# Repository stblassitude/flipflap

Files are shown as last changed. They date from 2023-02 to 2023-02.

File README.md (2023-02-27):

# Controller for OMEGA OM3021 Split-Flap Displays

# Overview
The controller board uses an D1 mini ESP8266 microcontroller to control a number of outputs going to the displays, and read inputs connected to the display encodes, which give the current position of the rotor with the split flaps.

The controller can address 8 lines and 15 columns, for a total of 120 characters. With the displays currently available to us, we're using 6 lines with 11 columns, for a total of 66 characters.

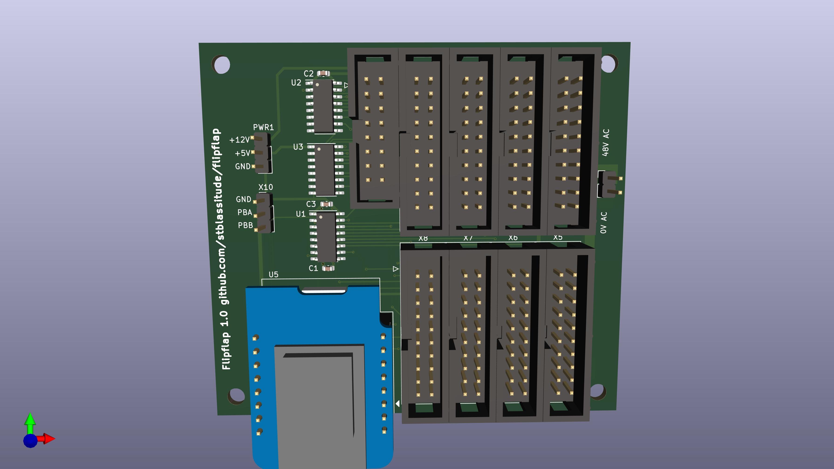
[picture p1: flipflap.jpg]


The schematic [flipflap-sch.pdf](flipflap-sch.pdf) and the assembly diagram [flipflap-pcb.pdf](flipflap-pcb.pdf) show the details of the board.

# Software
An Arduino sketch can be found in [arduino/flipflap](arduino/flipflap).

# Documentation OMEGA OM3021
Documentation for the split-flap display model can be found in [docs/](docs/). [Theory of Operation](docs/theory-of-operation.md) tries to explain how a microcontroller can control the displays.

# Arduino Setup

* https://arduino.github.io/arduino-cli/0.29/getting-started/
* https://medium.com/@thomas.kilmar/arduino-cli-with-visual-studio-code-on-macos-d2ad32ff0276

# Further Reading

We're not the only ones working with these modules.

* [Tim's SplitFlap Clock - Part I (Electronics)](https://web.archive.org/web/20220701175858/https://www.way2.net/2022/03/14/splitflap/). Unfortunately, the software part seems to never have been published.

# Version History

## 1.0

### Known Issues

* /ADC4 to /ADC7 are swapped when looking at the register outputs. This can easily be adjusted in the ADC cable.

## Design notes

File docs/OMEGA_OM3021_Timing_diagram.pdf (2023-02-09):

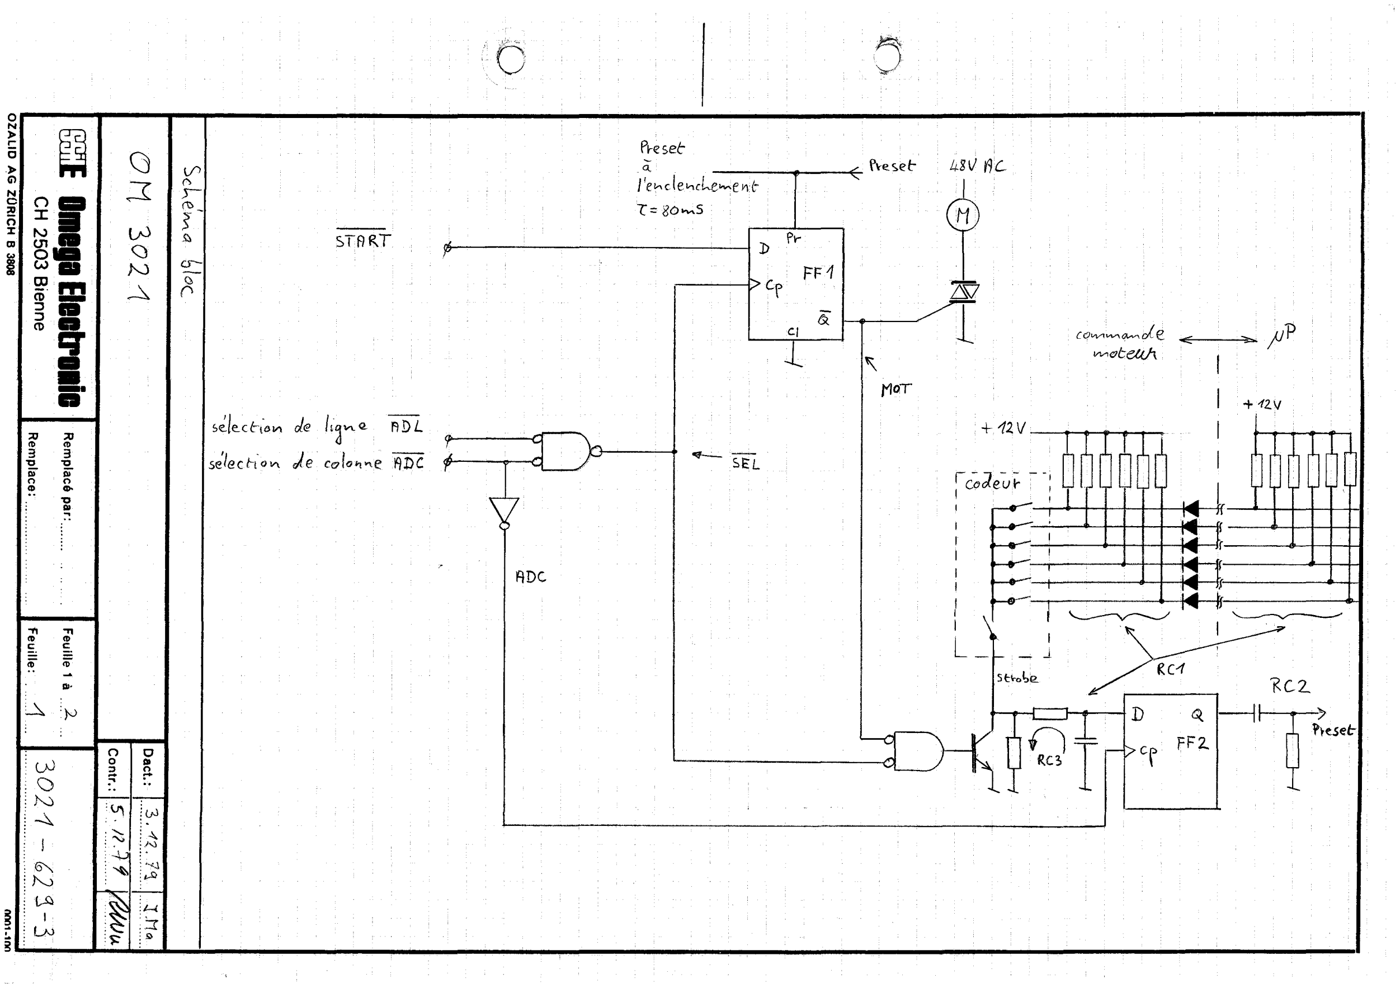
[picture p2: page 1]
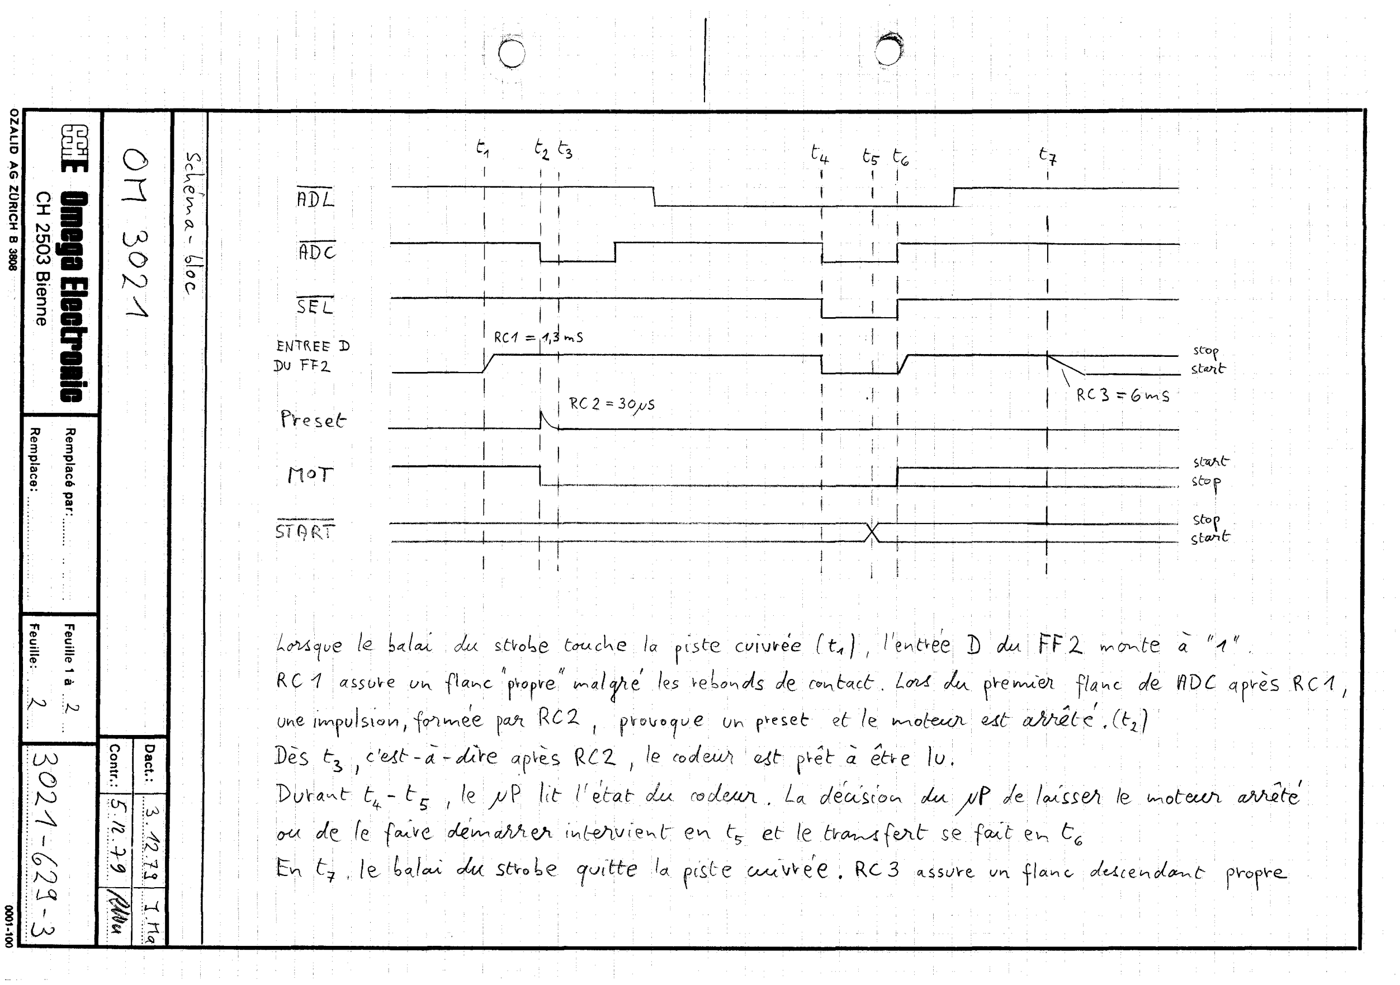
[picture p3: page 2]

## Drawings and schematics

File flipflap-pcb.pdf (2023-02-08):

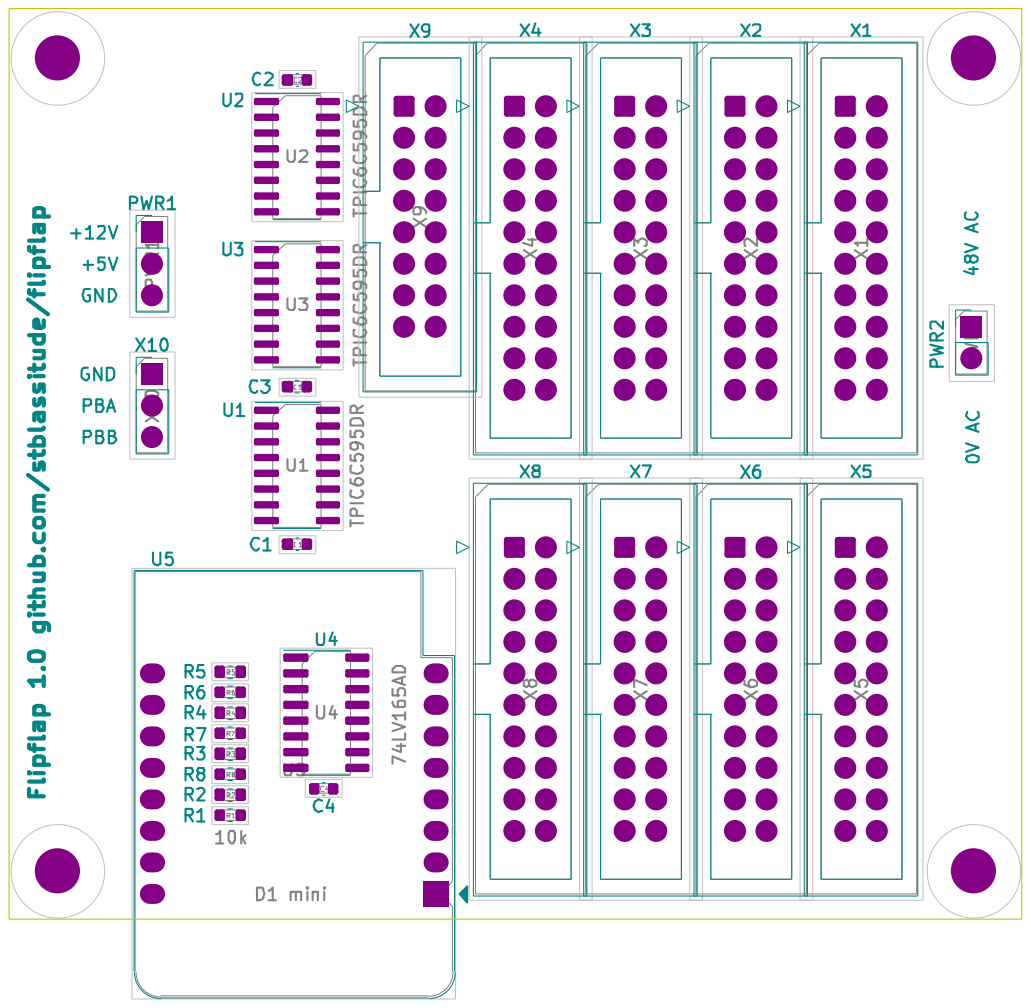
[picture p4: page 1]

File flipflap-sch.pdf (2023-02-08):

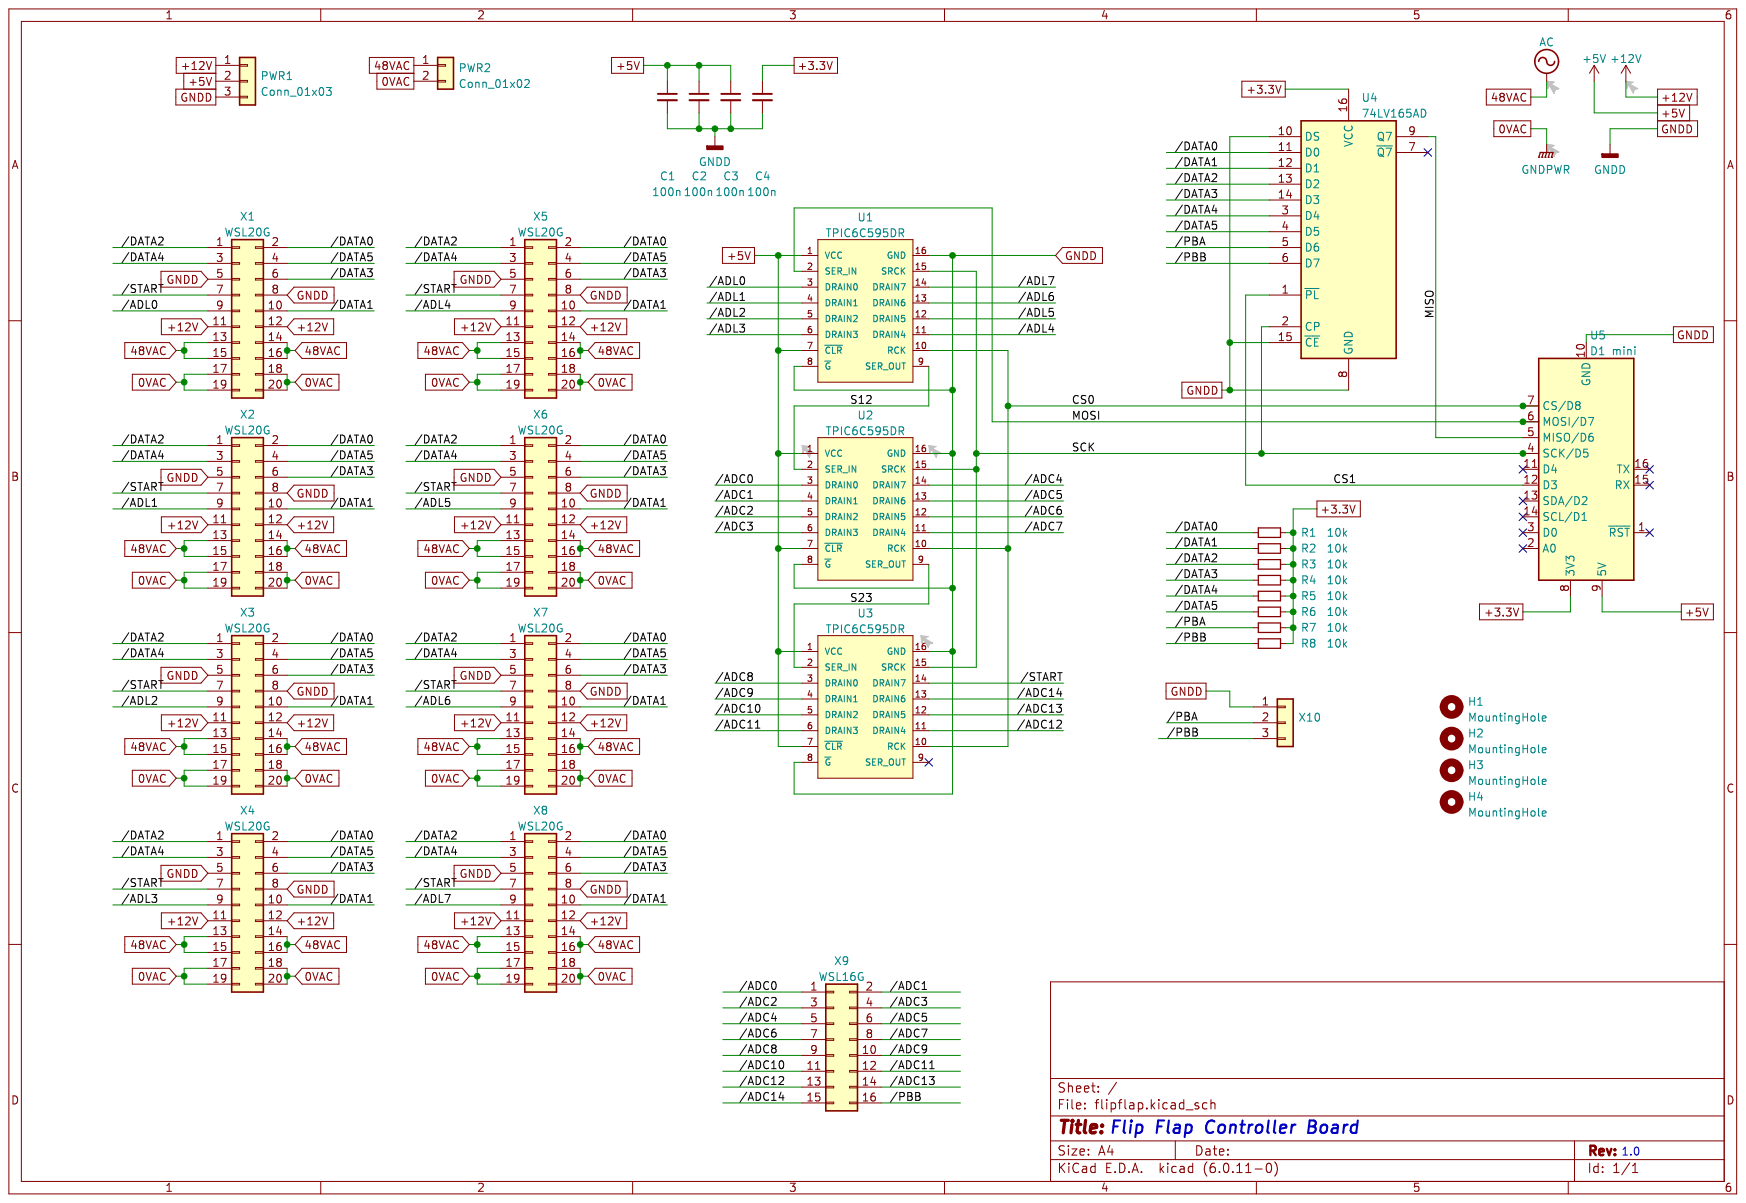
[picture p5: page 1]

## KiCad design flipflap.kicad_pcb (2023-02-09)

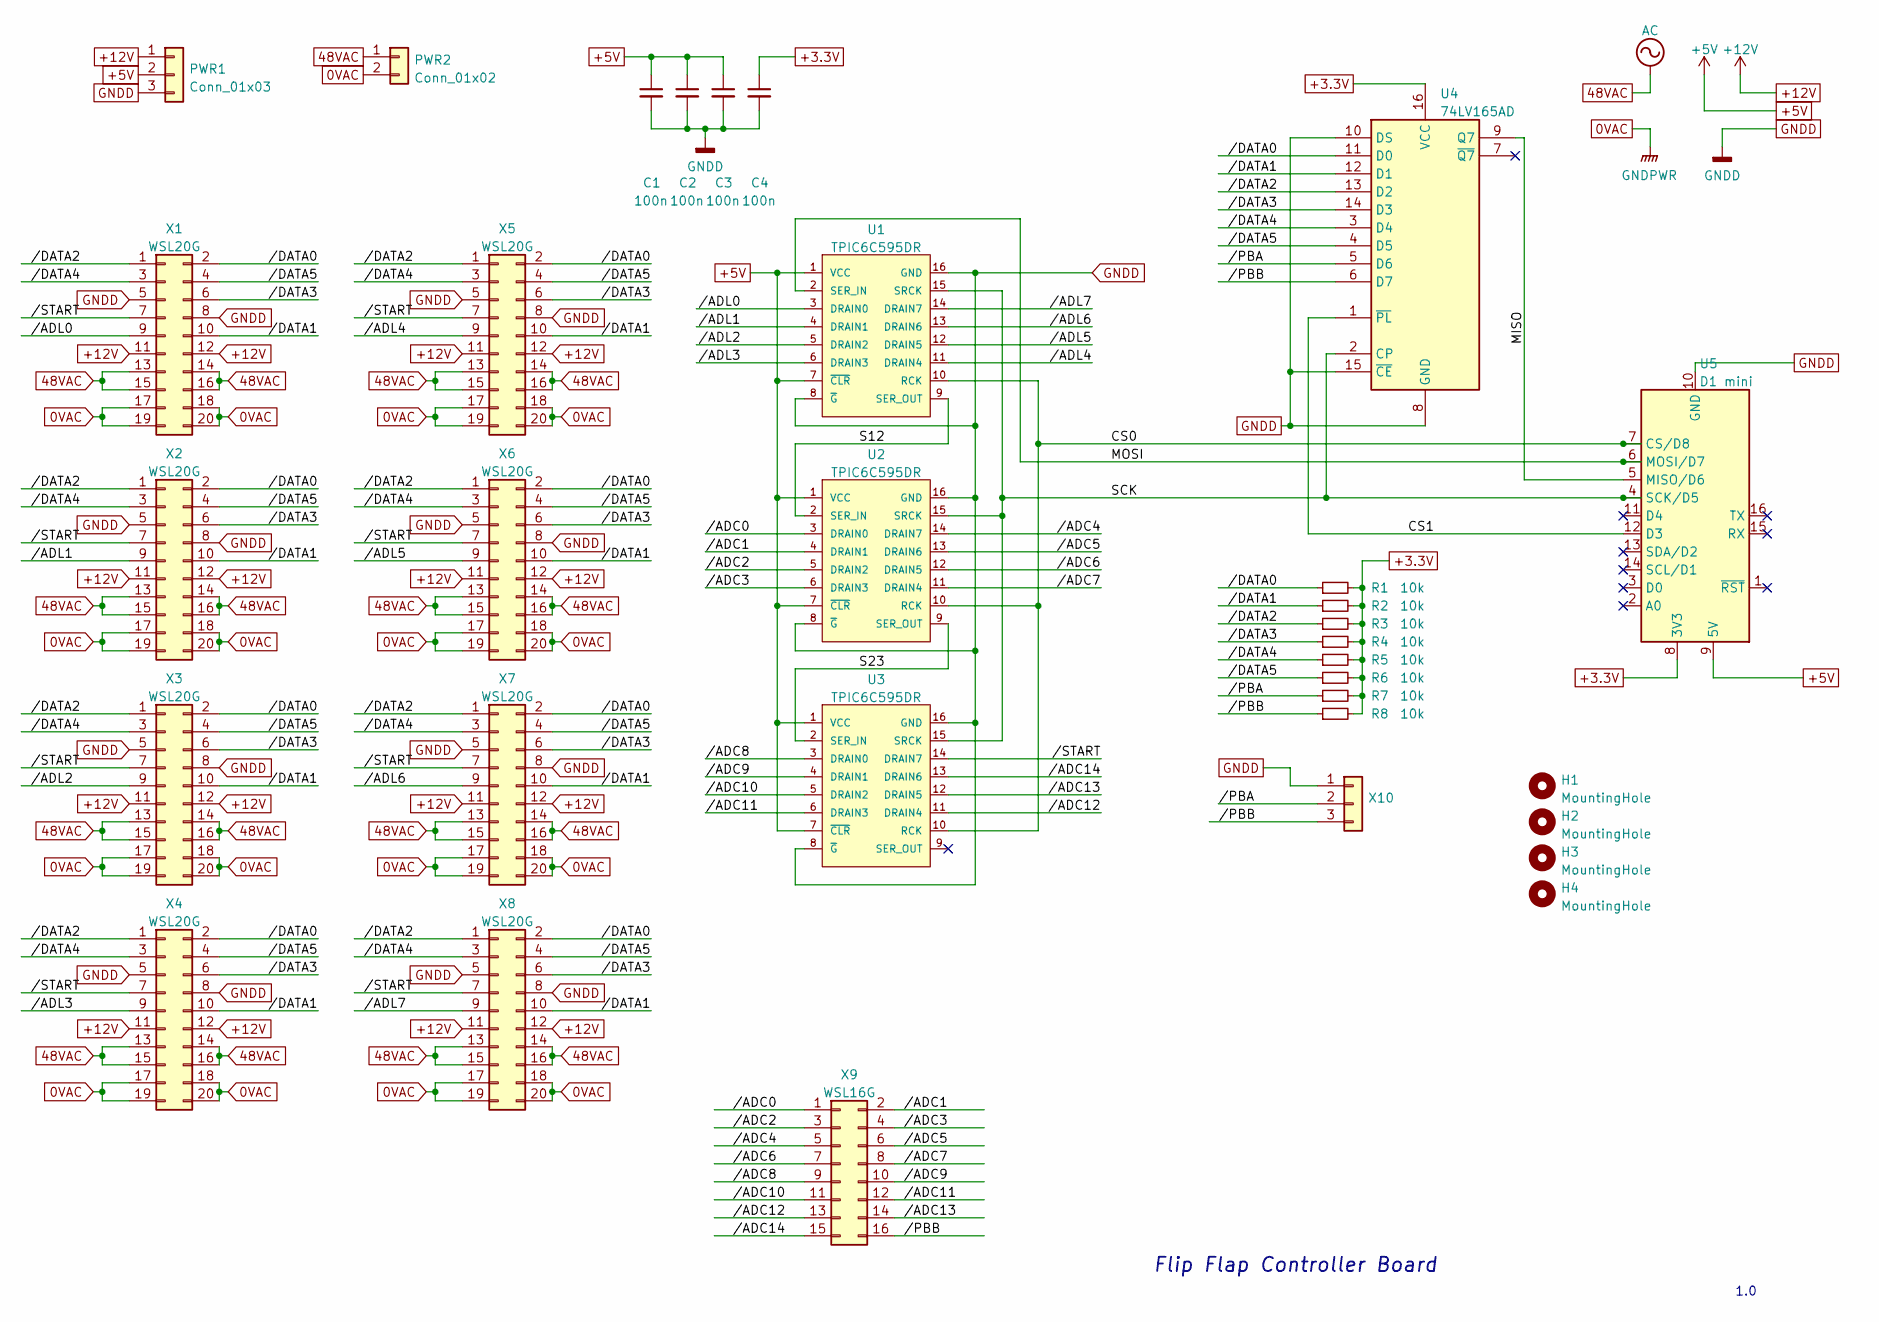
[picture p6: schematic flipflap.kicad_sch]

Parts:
C1, C2, C4: 100n; C_0603_1608Metric; JLCPCB C14663
C3: 100n; C_0603_1608Metric
H1, H2, H3, H4: MountingHole; MountingHole_3.5mm
PWR1: Conn_01x03; PinHeader_1x03_P2.54mm_Vertical
PWR2: Conn_01x02; PinHeader_1x02_P2.54mm_Vertical
R1, R2, R3, R4, R5, R6, R7, R8: 10k; R_0603_1608Metric; JLCPCB C4184
U1, U2, U3: TPIC6C595DR; SOIC-16_3.9x9.9mm_P1.27mm; JLCPCB C350572
U4: 74LV165AD; SOIC-16_3.9x9.9mm_P1.27mm; JLCPCB C478150
U5: D1 mini; WEMOS_D1_mini_light
X1, X2, X3, X4, X5, X6, X7, X8: WSL20G; IDC-Header_2x10_P2.54mm_Vertical
X9: WSL16G; IDC-Header_2x08_P2.54mm_Vertical
X10: Conn_01x03; PinHeader_1x03_P2.54mm_Vertical

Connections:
0VAC: PWR2.2, X1.17, X1.18, X1.19, X1.20, X2.17, X2.18, X2.19, X2.20, X3.17, X3.18, X3.19, X3.20, X4.17, X4.18, X4.19, X4.20, X5.17, X5.18, X5.19, X5.20, X6.17, X6.18, X6.19, X6.20, X7.17, X7.18, X7.19, X7.20, X8.17, X8.18, X8.19, X8.20
48VAC: PWR2.1, X1.13, X1.14, X1.15, X1.16, X2.13, X2.14, X2.15, X2.16, X3.13, X3.14, X3.15, X3.16, X4.13, X4.14, X4.15, X4.16, X5.13, X5.14, X5.15, X5.16, X6.13, X6.14, X6.15, X6.16, X7.13, X7.14, X7.15, X7.16, X8.13, X8.14, X8.15, X8.16
+3.3V: C4.1, R1.2, R2.2, R3.2, R4.2, R5.2, R6.2, R7.2, R8.2, U4.16 (VCC), U5.8 (3V3)
+5V: C1.1, C2.1, C3.1, PWR1.2, U1.1 (VCC), U1.7 (~CLR), U2.1 (VCC), U2.7 (~CLR), U3.1 (VCC), U3.7 (~CLR), U5.9 (5V)
+12V: PWR1.1, X1.11, X1.12, X2.11, X2.12, X3.11, X3.12, X4.11, X4.12, X5.11, X5.12, X6.11, X6.12, X7.11, X7.12, X8.11, X8.12
/CS0: U1.10 (RCK), U2.10 (RCK), U3.10 (RCK), U5.7 (CS/D8)
/CS1: U4.1 (~PL), U5.12 (D3)
/MISO: U4.9 (Q7), U5.5 (MISO/D6)
/MOSI: U1.2 (SER_IN), U5.6 (MOSI/D7)
/S12: U1.9 (SER_OUT), U2.2 (SER_IN)
/S23: U2.9 (SER_OUT), U3.2 (SER_IN)
/SCK: U1.15 (SRCK), U2.15 (SRCK), U3.15 (SRCK), U4.2 (CP), U5.4 (SCK/D5)
//ADC0: U2.3 (DRAIN0), X9.1
//ADC1: U2.4 (DRAIN1), X9.2
//ADC2: U2.5 (DRAIN2), X9.3
//ADC3: U2.6 (DRAIN3), X9.4
//ADC4: U2.14 (DRAIN7), X9.5
//ADC5: U2.13 (DRAIN6), X9.6
//ADC6: U2.12 (DRAIN5), X9.7
//ADC7: U2.11 (DRAIN4), X9.8
//ADC8: U3.3 (DRAIN0), X9.9
//ADC9: U3.4 (DRAIN1), X9.10
//ADC10: U3.5 (DRAIN2), X9.11
//ADC11: U3.6 (DRAIN3), X9.12
//ADC12: U3.11 (DRAIN4), X9.13
//ADC13: U3.12 (DRAIN5), X9.14
//ADC14: U3.13 (DRAIN6), X9.15
//ADL0: U1.3 (DRAIN0), X1.9
//ADL1: U1.4 (DRAIN1), X2.9
//ADL2: U1.5 (DRAIN2), X3.9
//ADL3: U1.6 (DRAIN3), X4.9
//ADL4: U1.11 (DRAIN4), X5.9
//ADL5: U1.12 (DRAIN5), X6.9
//ADL6: U1.13 (DRAIN6), X7.9
//ADL7: U1.14 (DRAIN7), X8.9
//DATA0: R1.1, U4.11 (D0), X1.2, X2.2, X3.2, X4.2, X5.2, X6.2, X7.2, X8.2
//DATA1: R2.1, U4.12 (D1), X1.10, X2.10, X3.10, X4.10, X5.10, X6.10, X7.10, X8.10
//DATA2: R3.1, U4.13 (D2), X1.1, X2.1, X3.1, X4.1, X5.1, X6.1, X7.1, X8.1
//DATA3: R4.1, U4.14 (D3), X1.6, X2.6, X3.6, X4.6, X5.6, X6.6, X7.6, X8.6
//DATA4: R5.1, U4.3 (D4), X1.3, X2.3, X3.3, X4.3, X5.3, X6.3, X7.3, X8.3
//DATA5: R6.1, U4.4 (D5), X1.4, X2.4, X3.4, X4.4, X5.4, X6.4, X7.4, X8.4
//PBA: R7.1, U4.5 (D6), X10.2
//PBB: R8.1, U4.6 (D7), X9.16, X10.3
//START: U3.14 (DRAIN7), X1.7, X2.7, X3.7, X4.7, X5.7, X6.7, X7.7, X8.7
GNDD: C1.2, C2.2, C3.2, C4.2, PWR1.3, U1.8 (~G), U1.16 (GND), U2.8 (~G), U2.16 (GND), U3.8 (~G), U3.16 (GND), U4.8 (GND), U4.10 (DS), U4.15 (~CE), U5.10 (GND), X1.5, X1.8, X2.5, X2.8, X3.5, X3.8, X4.5, X4.8, X5.5, X5.8, X6.5, X6.8, X7.5, X7.8, X8.5, X8.8, X10.1

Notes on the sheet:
Flip Flap Controller Board
1.0

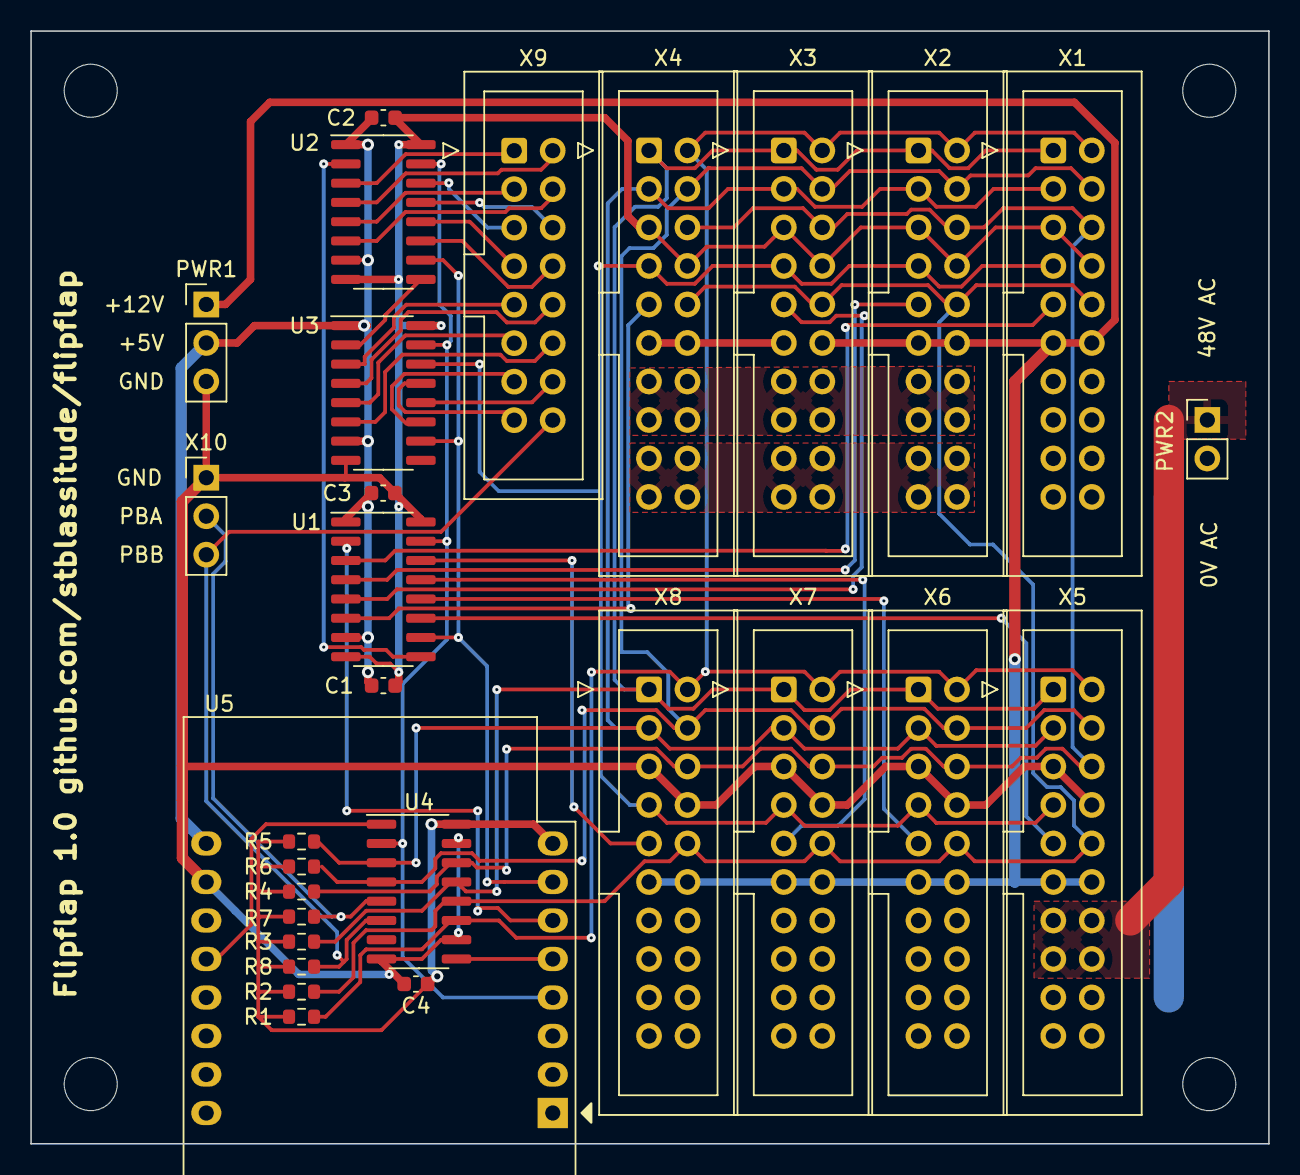
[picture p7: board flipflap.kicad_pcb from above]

Board: 2 copper layers, 81.7 x 73.4 mm, 33 parts (0 on the bottom side), 45 nets.

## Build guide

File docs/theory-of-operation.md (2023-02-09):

# OMEGA OM3021 Split Flap Display

## Theory of Operation

The [Timing Diagram](OMEGA_OM3021_Timing_diagram.pdf) has this description (translated from the original French):
> When the strobe brush touches the copper track (t1), the D input of FF2 goes up to "1". RC1 ensures a "clean" edge despite the contact bounces. At the first edge of ADC after RC1 an impulse, formed by RC2, causes a preset and the motor is stopped (t2).
> 
> From t3, i.e. after RC2, the encoder is ready to be read.
> 
> During t4-t5, the µP reads the encoder status. The decision of the µP to leave the motor stopped or to start it intervenes in t5 and the transfer is done in t6.
> 
> At t7 the strobe brush leaves the copper track. RC3 ensures a clean falling edge.

### Components and Circuit

This is a more detailed description of how the microcontroller controls the motor to move the display to the desired position.

One split-flap display consists of these components:
* The split flaps on their rotor
* A motor to drive the rotor
* An encoder that shows the position of the rotor, in this case, as an absolute 6 bit digital signal
* A control board helping to control the motor and read out the encoder

### Control Board
The control board ([schematics](OMEGA_OM3021_Schema.pdf)) is designed so that multiple displays can be connected on a bus. These signals are being used:
* Power: 0V/GND, 5V (logic), 12V (communications), 0VAC and 48V (motor)
* /START: start the motor (inverted)
* /ADL: selects a line (row) of displays (inverted)
* /ADC: selects a column of displays (inverted)
* /DATA0 to /DATA5: the output of the encoders

In a typical assembly, a number of displays are all connected to a bus, forming a line/row. Each individual display is selected through /ADC. Multiple rows can be connected together, as long as every row has its own /ADL. Using two 8 bit registers, it would be possible to address 8 rows with 8 displays each, for a total of 256 display. (Because of the length of the bus in this case, it is likely that capacitance of the cabling will require careful driving of the signals.)

All signals are on a 10x2 connector P3, except for /ADC, which is on P1.

While the control board uses 5V to supply the CD40xx series gates and flip-flops, the communication signals are all 12V. On the input side of the control board, /START, /ADL, and /ADC use a 27k/10k voltage divider with a 1N4148 protection diode to convert the 12V signal to something the CD40xx will tolerate. The /DATA signals are open collector driven to GND (see T4 and the encoder contacts), with a 1N4148 for each, allowing a separate logic level on the microcontroller side.

The control board controls the motor through triac T2, by decoding a number of signals from the microcontroller, and enabling the output of the encoder.

### Encoder
The encoder is an electro-mechanical device with seven circular copper tracks on a disc. All patterns are connected together. The disc is fixed to the rotor shaft. Six tracks indicate the absolute position of the rotor (either having copper or no copper in a particular position), while the strobe track alternates between copper and no copper inside each position. There are two encoder models, with either [40](OMEGA_OM3021_Codage_du_DIsque_40_pos.pdf) or [62](OMEGA_OM3021_Codage_du_DIsque_62_pos.pdf) positions. Note that each pattern has at least one of the data bits set, so that a connection is made between the strobe line and at least one data line.

### Moving the Rotor to the Desired Position

The microcontroller has to control stepping the rotor to the desired position. The [Timing Diagram](OMEGA_OM3021_Timing_diagram.pdf) contains both the timing and a schematic of the relevant parts; we reference some parts from the main [schematics](OMEGA_OM3021_Schema.pdf), in particular the RC circuits.

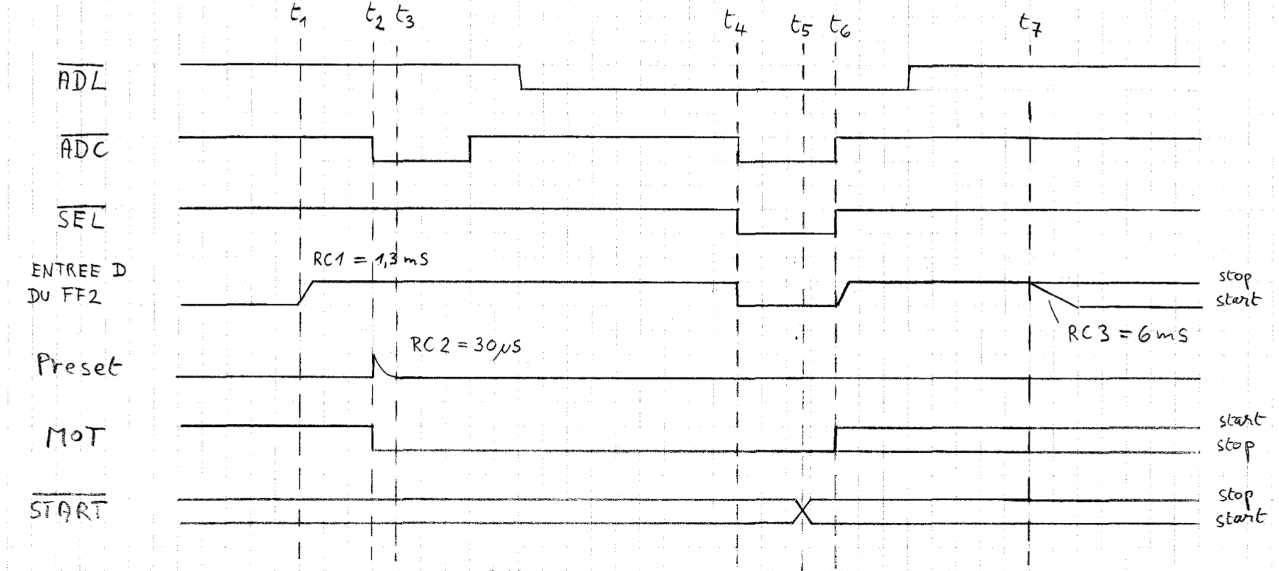
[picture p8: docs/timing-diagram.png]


Changing the rotor position starts from steady state and involves these steps in a loop:
1. The current position is obtained by asserting /ADL and /ADC (setting it low) to address the desired module, and then reading /DATA0 to /DATA5 (t<sub>4</sub>). T4 is on because /ADL and /ADC are low, and the motor is off, pulling STROBE, and therefor all data lines, to ground, leading to a low level on the data lines where they are present on the tracks.
2. If the position is the desired one, the micro controller keeps /START at high, and /ADL and/or /ADC are set high to deassert, and the loop ends.
3. The micro controller turns on the motor by pulling /START low (t<sub>5</sub>) while releasing /ADC (t<sub>6</sub>). This resets FF1, and turns on the motor. It also turns off T4, and clocks FF2, resetting it because the data input is low. The pull-ups on the data lines plus R4 and C3 form RC1, with a tau of 1.3ms, eventually leading to the data input in FF2 going high (right after t<sub>6</sub>).
4. As the rotor moves, the encoder will eventually leave the copper on the strobe track (t<sub>7</sub>). This will activate RC3 (C3, R4, R12, tau 6ms), and pull the data input of FF2 low. 
6. As the rotor continues to move, the strobe track will get back to copper (t<sub>1</sub>), pulling the data input of FF2 high again (RC1).
5. The micro controller repeatedly asserts /ADC, which clocks FF2. If the output from FF2 is high (t<sub>2</sub>), this starts RC2 (C4, R1, 0.3ms), creating a pulse on the internal PRESET line, setting FF1 and stopping the motor. (Editors note: it is unclear if the µC has to have good timing for the motor to advance to the exact position, or if it is sufficent to poll /ADC frequently, and rely on the contoller board to stop the motor at the correct time. It does seem though that missing the window where STROBE is connected will make the rotor advance to the next position.)
6. The loop then continues with checking if the desired position has been reached.

### Power on Reset

(Editors note: it is unclear if the controller is in a well defined state after power on. It might be necessary to run through the loop at least once to make sure the motor is off. T1, R2, and C1 look like they might be a reset circuit pulling PRESET high for 1µF\*1MΩ = 1s).

## Microcontroller Setup

The microcontroller needs these I/Os to control the displays:
* A number of 12V-tolerating open-collector outputs for /ADC to select the columns
* A number of 12V-tolerating open-collector outputs for /ADL to select the lines
* A 12V-tolerating open-collector output for /START
* 6 12V-tolerating inputs for /DATA0 to /DATA5

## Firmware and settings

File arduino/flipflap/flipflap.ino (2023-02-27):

#include <limits.h>
#include <stdio.h>

#include <CoopTask.h>
#include <ESP8266WiFi.h>
#include <SPI.h>
#include <WiFiManager.h> 

#define NCOLS 11
#define NROWS 1
#define DEBUG 0

volatile byte desired_position[NCOLS][NROWS];
volatile byte current_position[NCOLS][NROWS];

/**
 * Maps ISO-8859-1 characters (char) to their position on the display (index). Of the 64 encodings, 0 and 63 are not used; they are encoded as \0.
 */
const char lookup[64] = 
  "\000\xdc\xd8\xc4\xd6:98"
  "76543210"
  "/.-,!?)("
  "=;      "
  "     ZYX"
  "WVUTSRQP"
  "ONMLKJIH"
  "GFEDCBA"; // implicit \0 at end because of quoted string

byte outputs[3];
byte input;

#if DEBUG!=0
#define debug(...) Serial.printf(__VA_ARGS__);
#else
#define debug(...)
#endif

/**
 * Copies the output bits to the output shift registers.
 */
void update_outputs() {
  SPI.beginTransaction(SPISettings(32000000, MSBFIRST, SPI_MODE0));
  for (int i = 4; i--; ) {
    SPI.transfer(outputs[i]);
  }
  SPI.endTransaction();
  digitalWrite(D8, HIGH);
  delayMicroseconds(10);
  digitalWrite(D8, LOW);  
  delayMicroseconds(10);
}

/**
 * Copies the input shift register into the input bits.
 * 
 * @returns the input value
 */
byte read_input() {
  byte r;
  SPI.beginTransaction(SPISettings(32000000, MSBFIRST, SPI_MODE0));
  digitalWrite(D3, LOW);
  delayMicroseconds(10);
  digitalWrite(D3, HIGH);
  delayMicroseconds(10);
  r = SPI.transfer(0x3a);
  SPI.endTransaction();
  // There is a (hardware) bug that makes the 165 shift early, loosing the MSB, and adding a 0 at the end.
  // We can ignore the 8th bit/PBB and simply shift back down here.
  input = r >> 1;
  return input;
}


/**
 * De-selects all columns, lines, and start.
 */
void select_none() {
  outputs[0] = 0;
  outputs[1] = 0;
  outputs[2] = 0;
}

/**
 * Select one ADL.
 * 
 * @param line ADL to select, 0-7.
 */
void select_line(int line) {
  if (line >= 0 && line <= 7)
    outputs[0] |= 1 << line;
}

/**
 * Select one ADC.
 * 
 * @param column ADC to select.
 */
void select_column(int column) {
  if (column < 0 || column > 14) {
    return;
  } else if (column < 8) {
    outputs[1] |= 1 << column;
  } else {
    outputs[2] |= 1 << (column - 8);
  }
}

/**
 * Select all columns at once. This is mainly used to top all motors.
 */
void select_all_columns() {
  outputs[1] = 0xff;
  outputs[2] = 0x7f;
}

/**
 * Returns true if at least one line or column is selected
 * 
 * @returns true if any line or column is selected
 */
int any_selected() {
  return outputs[0] || outputs[1] || outputs[2];
}

/**
 * Set the START line.
 * 
 * @param start 1 to start
 */
void set_start() {
  outputs[2] = outputs[2] | 0x80;
}


/**
 * Trigger motor stop. We wait half a half-cycle for all motors to come to a halt.
 */
void stop_all() {
    select_none();
    update_outputs();
    delay(50);
    select_all_columns();
    update_outputs();
    delay(20);
    select_none();
    update_outputs();
}

/**
 * Update the current position of the display identified by col and row.
 * 
 * @param col the column
 * @param row the row
 */
int read_col_row(int col, int row) {
  int p = 63;
  int matches = 5; // a number of consecutive identical reads should be reliable
  for (int i = 10; i--; ) {
    select_none();
    update_outputs();
    delay(2);
    select_column(col);
    select_line(row);
    update_outputs();
    delay(5);
    current_position[col][row] = read_input() & 0x3f;
    if (current_position[col][row] != 63 && current_position[col][row] == p)
      matches--;
    if (matches <= 0)
      break;
    p = current_position[col][row];
  }
  return current_position[col][row];
}

int char_to_position(char c) {
  for (int i = 64; i--; ) {
    if (c == lookup[i])
      return i;
  }
  return 63;
}

char position_to_char(int p) {
  if (p == 0 || p == 63)
    return '_';
  return lookup[p];
}

/**
 * Dump all the bits to the serial console.
 */
void print_state() {
  static int count = 0;

  if (count % 16 == 0) {
    Serial.println("Line____________________   Column_____________________________________  St  Data_____________  Pos");
    Serial.println("  0  1  2  3  4  5  6  7   0  1  2  3  4  5  6  7  8  9 10 11 12 13 14  rt   0  1  2  3  4  5");
  }
  for (int i = 0; i < 8; i++) {
    Serial.printf("  %c", ((outputs[0] >> i) & 1) ? 'X' : '.');
  }
  Serial.print(" ");
  for (int i = 0; i < 8; i++) {
    Serial.printf("  %c", ((outputs[1] >> i) & 1) ? 'X' : '.');
  }
  for (int i = 0; i < 7; i++) {
    Serial.printf("  %c", ((outputs[2] >> i) & 1) ? 'X' : '.');
  }
  Serial.printf("   %c ", ((outputs[2] >> 7) & 1) ? 'X' : '.');
  for (int i = 0; i < 6; i++) {
    Serial.printf("  %c", ((input >> i) & 1) ? 'X' : '.');
  }
  Serial.printf("  %2d", input & 0x3f);
  Serial.println("");
  count++;
}

/**
 * Dump the state to the serial console.
 */
void print_control_status() {
#if DEBUG!=0
  Serial.print("Desired: ");
  for (int col = 0; col < NCOLS; col++) {
    for (int row = 0; row < NROWS; row++) {
      int p = desired_position[col][0];
      Serial.printf("%c (%3d), ", position_to_char(p), p);
    }
  }
  Serial.print("\nCurrent: ");
  for (int col = 0; col < NCOLS; col++) {
    for (int row = 0; row < NROWS; row++) {
      int p = current_position[col][0];
      Serial.printf("%c (%3d), ", position_to_char(p), p);
    }
  }
  Serial.println("");
#endif
}

/**
 * Compute the waiting time for a display to reach the desired position from the current one.
 * 
 * @param col the column
 * @param row the row
 * @return absolute millis after which the motor should be stopped.
 */
long compute_deadline(int col, int row) {
  int distance = current_position[col][row] - desired_position[col][row];
  if (distance < 0)
    distance += 62;
    debug("  distance %d/%d = %d-%d = %d\n", col, row, current_position[col][row], desired_position[col][row], distance);
  return (4500 * distance / 62) - 50; // experimentally determined
}

/**
 * Start and stop the motor quickly. This is used if the motor stopped, but no position can be read.
 * 
 * @param col the column
 * @param row the row
 */
void nudge(int col, int row) {
  select_none();
  update_outputs();
  select_column(col);
  select_line(row);
  set_start();
  update_outputs();
  delay(5);
  select_none();
  update_outputs();
}

String escapeHtml(String s) {
  String r = "";
  for (int i = 0; i < s.length(); i++) {
    char c = s.charAt(i);
    switch (c) {
      case '\'':
        r += "&apos;";
        break;
      case '"':
        r += "&quot;";
        break;
      case '<':
        r += "&lt;";
        break;
      case '&':
        r += "&amp;";
        break;
      default:
        r += c;
    }
  }
  return r;
}

void updateText(String s) {
  s.trim();
  if (s.equals("^")) {
    Serial.println("Stopping...");
    for (int col = 0; col < NCOLS; col++) {
      for (int row = 0; row < NROWS; row++) {
        desired_position[col][row] = 63;
      }
    }
    stop_all();
  } else if (s.charAt(0) == '*') {
      s.setCharAt(0, ' ');
      int p = s.toInt();
      for (int col = 0; col < NCOLS; col++) {
        for (int row = 0; row < NROWS; row++) {
          desired_position[col][row] = p;
        }
      }
  } else {
    int space = char_to_position(' ');
    int i = 0;
    for (int col = 0; col < NCOLS; col++) {
      for (int row = 0; row < NROWS; row++) {
        desired_position[col][row] = space;
      }
    }
    s.toUpperCase();
    Serial.printf("Updating \"%s\"\n", s);
    for (int col = 0; col < NCOLS && i < s.length(); col++) {
      for (int row = 0; row < NROWS && i < s.length(); row++) {
        int p;
        do {
          p = char_to_position(s.charAt(i++));
        } while (p <= 0 && p >= 63 && i < s.length());
        if (p > 0 && p < 63) {
          desired_position[col][row] = p;
        }
      }
    }
  }
}

/**
 * Main control loop for starting and stopping the motors of the displays.
 */
void control_displays() {
  int deadline;
  Serial.println("Starting control loop");
  stop_all();
  int space = char_to_position(' ');
  for (int col = 0; col < NCOLS; col++) {
    for (int row = 0; row < NROWS; row++) {
      desired_position[col][row] = space;
      read_col_row(col, row);
    }
  }

  for (;;) {
    int running;

    yield();
    deadline = INT_MAX;
    running = 0;
    for (int col = 0; col < NCOLS; col++) {
      // start motors on any display not in the correct position
      for (int row = 0; row < NROWS; row++) {
        if (desired_position[col][row] != 63 && desired_position[col][row] != current_position[col][row]) {
          int dl = compute_deadline(col, row);
          if (dl < deadline) {
            deadline = dl;
          }
          debug("  starting %d/%d, dl %d\n", col, row, dl);
          select_none();
          update_outputs();
          select_column(col);
          select_line(row);
          delay(5);
          set_start();
          update_outputs();
          delay(5);
          select_none();
          set_start();
          update_outputs();
          running = 1;
        }
      }
    }
    if (!running) {
      delay(50); // nothing to do, give time to other tasks
      continue;
    }
    print_control_status();

    debug("  deadline %d\n", deadline);
    delay(deadline);
    do {
      running = 0;
      debug("  reading\n");
      stop_all();
      for (int col = 0; col < NCOLS; col++) {
        for (int row = 0; row < NROWS; row++) {
          read_col_row(col, row);
          if (desired_position[col][row] != 63 && current_position[col][row] == 63)
            running = 1;
        }
      }
      print_control_status();
      select_none();
      if (running) {
        for (int col = 0; col < NCOLS; col++) {
          for (int row = 0; row < NROWS; row++) {
            if (desired_position[col][row] != 63 && current_position[col][row] == 63) {
              // not yet in reading position, quickly start it up and stop it right away again
              debug("  nudge %d/%d\n", col, row);
              nudge(col, row);
              print_control_status();
            }
          }
        }
      }
    } while (running);
    debug("  done nudging\n");
    print_control_status();
  }
}

/**
 * Accept and process input on the serial console.
 */
void console_input() {
  String s;
  for (;;) {
    delay(1);
    if (!Serial.available()) {
      yield();
      continue;
    }
    s = Serial.readString();
    if (s.length() > 0) {
      updateText(s);
    }
  }
}


/**
 * Blink the LED so we know the controller is still running.
 */
void heartbeat() {
  pinMode(LED_BUILTIN, OUTPUT);

  for (;;) {
    digitalWrite(LED_BUILTIN, LOW);
    delay(200);
    digitalWrite(LED_BUILTIN, HIGH);
    delay(800);
  }
}


BasicCoopTask<CoopTaskStackAllocatorAsMember<2000>> heartbeatTask("heartbeat", heartbeat);
BasicCoopTask<CoopTaskStackAllocatorAsMember<2000>> inputTask("input", console_input);
BasicCoopTask<CoopTaskStackAllocatorAsMember<2000>> controlTask("control", control_displays);

WiFiManager wifiManager;

ESP8266WebServer server(80);


void setupWifi() {
  Serial.print("\n\nConnecting to WiFi...");
  char apname[64];
  sprintf(apname, "flipflap-%02x%02x%02x", WiFi.macAddress()[3], WiFi.macAddress()[4], WiFi.macAddress()[5]);
  wifiManager.autoConnect(apname);

  while (WiFi.status() != WL_CONNECTED) {
    delay(500);
    Serial.print(".");
  }
  Serial.println();

  Serial.print("Connected, IP address: ");
  Serial.println(WiFi.localIP());
}

void setupWebserver() {
  server.onNotFound([]() {
    String message = "File Not Found\n\n";
    message += "URI: ";
    message += server.uri();
    message += "\nMethod: ";
    message += (server.method() == HTTP_GET) ? "GET" : "POST";
    message += "\nArguments: ";
    message += server.args();
    message += "\n";
    for (uint8_t i = 0; i < server.args(); i++) { message += " " + server.argName(i) + ": " + server.arg(i) + "\n"; }
    server.send(404, "text/plain", message);
  });
  server.on("/", [](){
    String text = "CCC HH";
    for (int i = 0; i < server.args(); i++) {
      if (server.argName(i) == "text") {
        text = server.arg(i);
        updateText(text);
      }
    }
    server.send(200, "text/html", 
    "<html><head><meta charset='ISO-8859-1'><title>Flip Flap</title></head><body><h1>Flip Flap</h1>"
        "<form>"
        "<input type='text' name='text' value='"
      + escapeHtml(text) 
      + "'>"
        "<input type='submit'>"
        "</form>"
        "</body></html>");
  });
  server.begin();
}

void setup() {
  Serial.begin(230400);
  SPI.begin();
  SPI.setHwCs(false);

  pinMode(D8, OUTPUT); // RCLK for output shift registers
  digitalWrite(D3, LOW); 
  pinMode(D3, OUTPUT); // /PL for input shift register
  digitalWrite(D5, HIGH); 
  
  for (int i = 10; i--; )
    stop_all();

  setupWifi();
  setupWebserver();
    
  heartbeatTask.scheduleTask();
  inputTask.scheduleTask();
  controlTask.scheduleTask();

  Serial.println("\n\nReady");
}


void loop() {
  runCoopTasks();
  server.handleClient();
}

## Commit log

2023-02-06 First draft of the schematics for the new controller board
    [flipflap.kicad_pcb, flipflap.kicad_sch]
2023-02-06 Add footprints to all parts
    [flipflap.kicad_sch]
2023-02-07 Completed PCB, populated on both sides.
    [flipflap.kicad_pcb, flipflap.kicad_sch]
2023-02-08 Complete PCB with components only on one side, some corrections included
    [flipflap.kicad_pcb, flipflap.kicad_sch]
2023-02-09 As ordered from JLCPCB
    [flipflap.kicad_pcb, flipflap.kicad_sch]
2023-02-27 First draft of an Arduino sketch to control the displays.
